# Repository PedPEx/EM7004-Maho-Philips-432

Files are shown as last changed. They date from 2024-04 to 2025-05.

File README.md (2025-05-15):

# EM7004-Maho-Philips-432 (ABORTED)
Retrofit analog interface adaptor for Maho CNC machines with a Philips 432/10 controller for use with a [Beckhoff EM7004](https://www.beckhoff.com/de-de/produkte/i-o/ethercat-klemmen/el-elm7xxx-kompakte-antriebstechnik/em7004.html) 

This project is used in the [Maho400E-LinuxCNC Retrofit project](https://github.com/PedPEx/Maho400E-LinuxCNC).

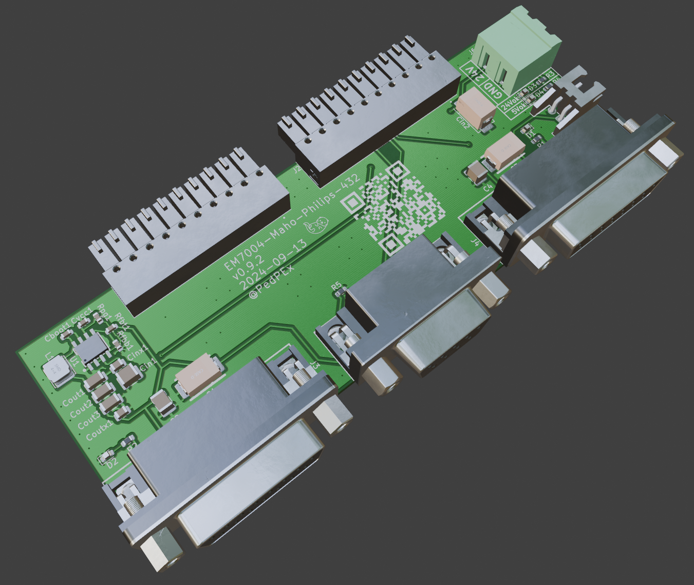
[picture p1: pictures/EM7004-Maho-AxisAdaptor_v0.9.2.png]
v0.9.2 Blender render v0.9.2


## Archiving
This project is being archived due to the EM7004 just having a 16 bit wide counter. With a travel-path of up to ~400 mm with a resolution of 1 µm a counter of at least 
```math 
n_{min} = \log_2 (\frac{400 mm}{1 \mu m}) = 18.61 bit \approx 19 bit 
```
The functionality of the rest of the PCB was not tested (BuckConverter is working). I'm sorry for everyone who had high hopes for this project or planned to use the finished product.

## Milestones
accomplished Milestones / ToDo:
- ✅ ready to go prototype at hand (v0.9.2 - corrected)
- ✅ working buck converter
- 🔲 tested with Maho axis attached
    - 🔲 working glass scale readout
    - 🔲 working Indramat speed controll

## Powering
The board needs a seperate supply voltage input to power the Philips converter-board (similar to Heidenhain EXE) for the encoders. The 5 V regulator is based around a [Texas Instruments LM33630](https://www.ti.com/product/LMR33630) and onboard. The BuckConverter part is based on the design from this [repository](https://github.com/PedPEx/BuckConverter_Enable). I recommend the [Phoenix Contact - 1962600 - TFKC 2,5/ 2-ST-5,08](https://www.phoenixcontact.com/de-de/produkte/leiterplattenstecker-tfkc-25-2-st-508-1962600) connectors to simply daisy chain all EM7004 24 V power supply lines.

## Usage
The pcb can be pretty easily assembled with standard parts of of LCSC (for furter information look at the [Online BOM](#online-preview--bom)). The connectors on the other side for plugging into the Beckhoff Module on the other hand are somewhat special. Unfortunately i found not a single alternative to the [Phoenix Contact - 1830498 - IMC 1,5/10-G-3,5 P20 THR](https://www.phoenixcontact.com/de-de/produkte/leiterplattengrundleiste-imc-1510-g-35-p20-thr-1830498) connectors, and these are not cheap at all. You can get five of them for free for testing purposes.

The first batch of boards is used in the testbench for the [Maho400E-LinuxCNC Retrofit project](https://github.com/PedPEx/Maho400E-LinuxCNC). LCSC did have a fault in the footprint files of the DB15 connectors, they were mirrored by accident. The fault has been fixed in v0.9.3 and the connectors were placed on the underside of the PCB in order to test the boards for functionality.

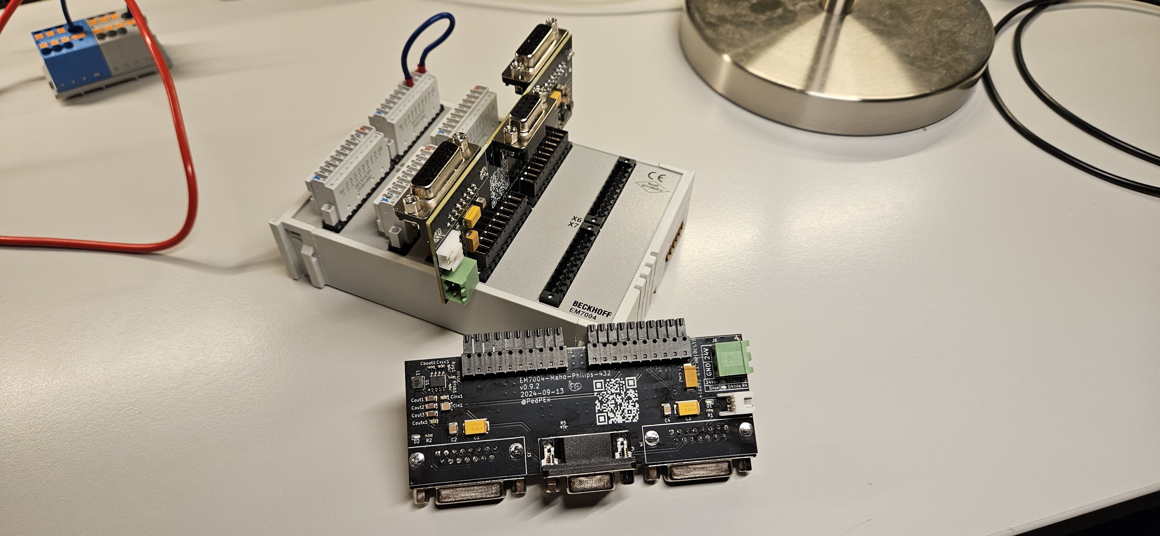
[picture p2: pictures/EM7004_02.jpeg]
EM7004_03

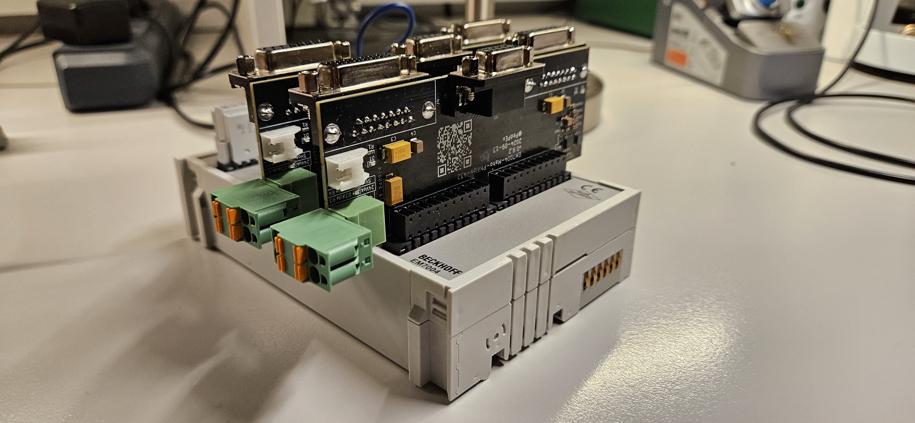
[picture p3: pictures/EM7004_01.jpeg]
EM7004_02

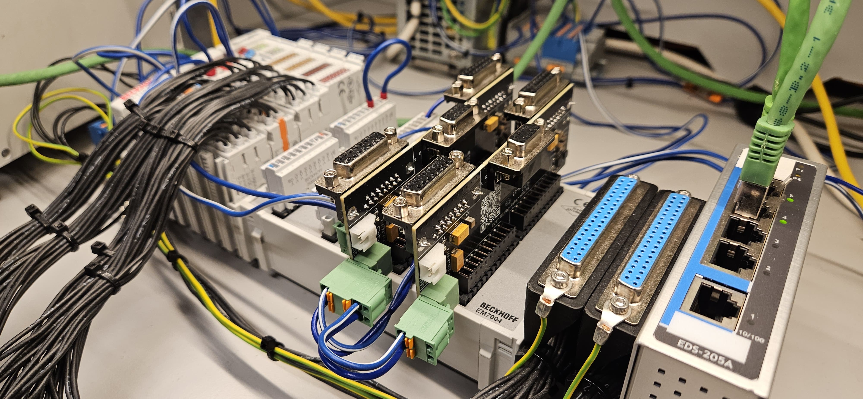
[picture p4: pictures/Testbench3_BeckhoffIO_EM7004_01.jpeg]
Testbench3_EM7004_01


## Saving costs
In order to save some money, a JST right beside the 24V input connector is provided to power other adaptors and not needing an additional buck converter onboard of the other PCBs. Just daisy chain all adaptor interfaces. The BOM needs to be adjusted accordingly for that use case (ToDo).

## Limitations
In our Maho 400E with the original Philips 432/10 controller the encoder converter card is labeled "Maho 27.69 658" on the top and no label on the bottom. It seems to be a standard Heidenhain part (Part#: 229 281 01). Example pictures are avaliable [here](https://www.cnc-shopping.com/en/philips-432-cnc-heidenhain-229-281-01-exe-platine-maho-27-69-658-3-axis-615dc0edd3849-p-5395.html). This project is specifically meant to be used with this MAHO part!

Keep in mind this adaptor is not suited for use with a standard [Heidenhain EXE 600/900](https://cncbote.de/artikel/heidenhain-exe-600-5-f-id-nr-172680a/) series converter. These need an extra 12 V supply and other connectors.

## Online Preview / BOM / Schematic
[Online BOM](https://htmlpreview.github.io/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)

[PDF Schematic](https://github.com/PedPEx/EM7004-Maho-Philips-432/blob/main/EM7004-Maho-AxisAdaptor.pdf)

## Software part
This board is meant to be used with a EM7004 module and LinuxCNC. The LinuxCNC software part can be found here: [Maho400E-LinuxCNC](https://github.com/PedPEx/Maho400E-LinuxCNC)

## Note
The pictures were rendered with the help of Blender and the [pcb2blender](https://github.com/30350n/pcb2blender) plugin and the HTML BOM was created with [InteractiveHtmlBom](https://github.com/openscopeproject/InteractiveHtmlBom).

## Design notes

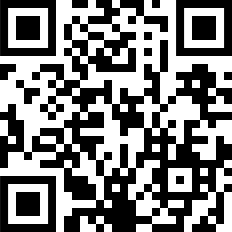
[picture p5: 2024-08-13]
pictures/QR.png

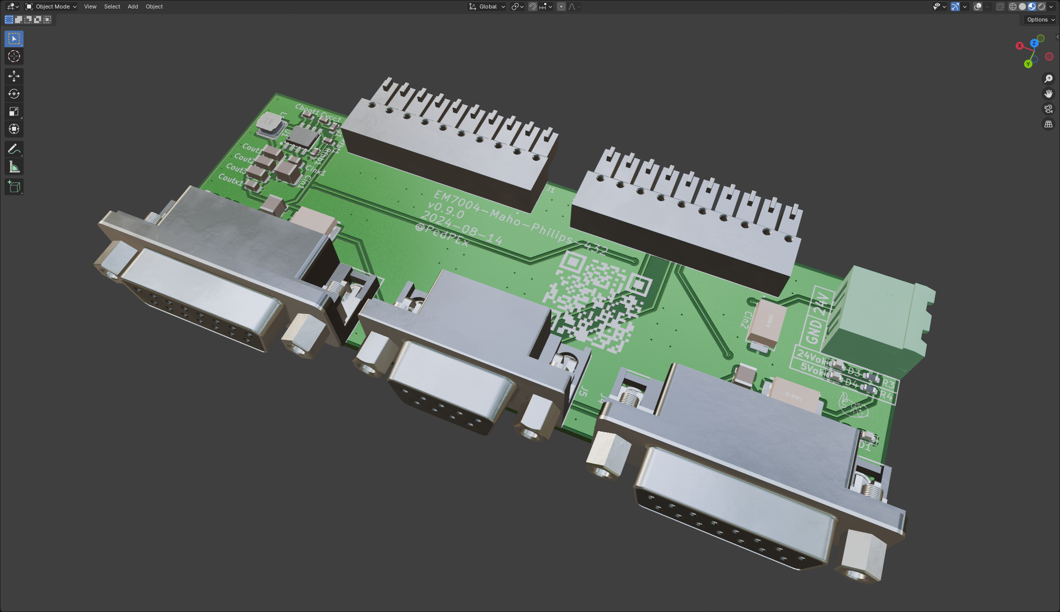
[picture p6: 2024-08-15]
pictures/EM7004-Maho-AxisAdaptor1.png

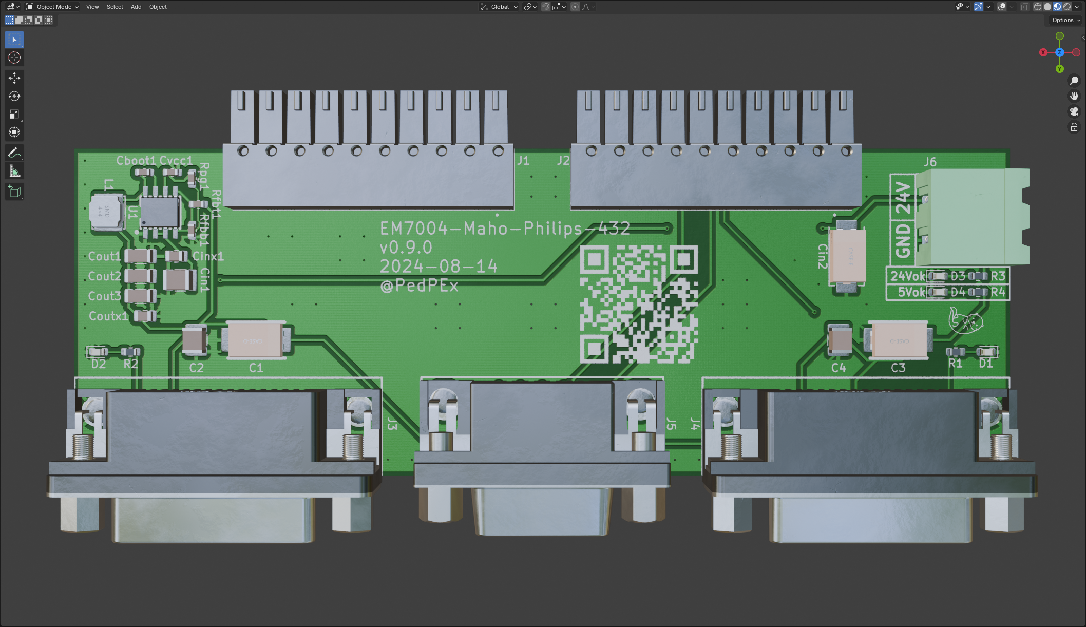
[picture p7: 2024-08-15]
pictures/EM7004-Maho-AxisAdaptor.png

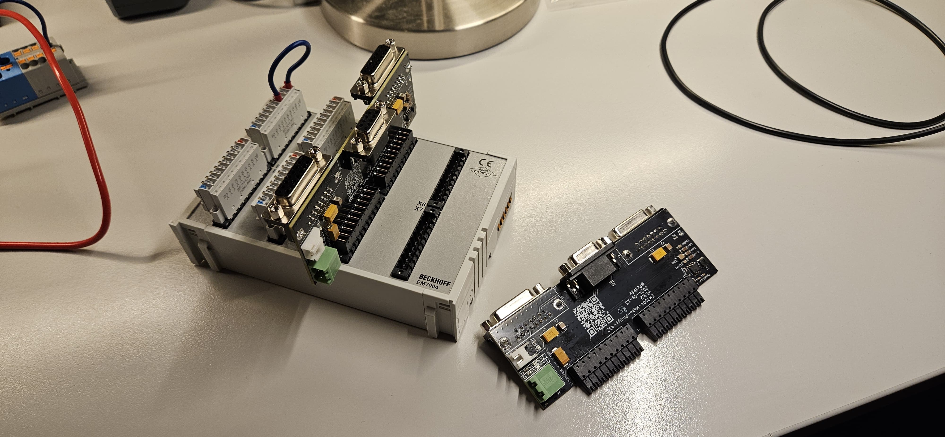
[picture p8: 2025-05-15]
pictures/EM7004_03.jpeg

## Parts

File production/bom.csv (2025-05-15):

Designator | Footprint | Quantity | Value | LCSC Part #
C1, C3 | CASE-D_7343 | 2 | 100u | C8025
C2, C4, Cin1 | 1210 | 3 | 10u | C138687
Cboot1 | 0603 | 1 | 100n | C14663
Cin2 | CAP-SMD_L7.3-W4.3-R-RD | 1 | 10u | C117038
Cinx1 | 0805 | 1 | 220n | C5378
Cout1, Cout2, Cout3 | 1206 | 3 | 47u | C412300
Coutx1 | 0805 | 1 | 100n
Cvcc1 | 0603 | 1 | 1u | C5199872
D1, D2, D3, D4 | 0603 | 4 | LED
J00, J10 | PHOENIX_1830498 | 2 | 1830498
J01, J11 | DSUB-TH_XUNPU_D-SUB-DR-15PCM-CB | 2 | D-SUB-DR-15PCM-CB | C19077338
J2 | DSUB-TH_DMR-9S | 1 | DMR-9S | C141882
J3 | CONN-TH_2P-P5.08_XY2500R-D5.08-2P | 1 | XY2500R-D-5.08-2P | C505824
J4 | CONN-TH_S2B-XH-A-1-LF-SN | 1 | S2B-XH-A-1 (LF)(SN) | C163035
L1 | IND-SMD_L4.0-W4.0 | 1 | APSWPA4018S100MTF | C5363859
R1, R2, R4 | 0603 | 3 | 680
R3 | 0603 | 1 | 4k7
R5 | 0603 | 1 | 0R
Rfbb1 | 0603 | 1 | 24k9 | C25962
Rfbt1, Rpg1 | 0603 | 2 | 100k | C25803
U1 | ESOP-8_L4.9-W3.9-P1.27-LS6.0-TL-EP | 1 | LMR33630ADDAR | C841384

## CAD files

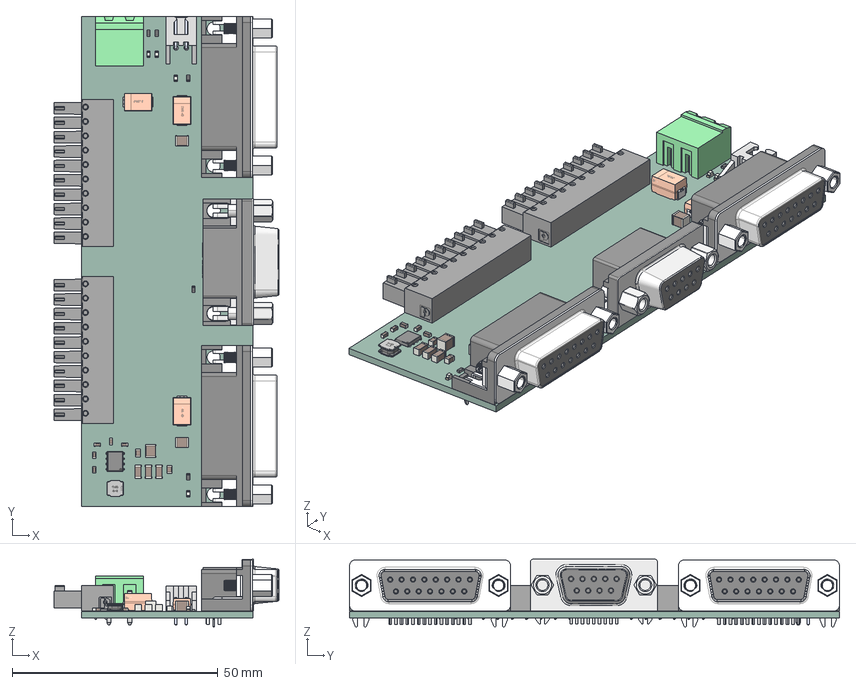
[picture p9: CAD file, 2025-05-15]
EM7004-Maho-AxisAdaptor_v093.step
54.6 x 119.2 x 16.4 mm
C_0603_1608Metric x 5
C_1206_3216Metric x 3
R_0603_1608Metric x 5
ESOP-8_L4.9-W3.9-P1.27-LS6.0-TL-EP
C_1210_3225Metric x 3
LED_0603_1608Metric x 4
C_0805_2012Metric x 2
IND-SMD_L4.0-W4.0-H1.9
DSUB-TH_DMR-9S
CASE-E_L7.3-W4.3-H4.1
CONN-TH_S2B-XH-A-1-LF-SN
CASE-D_L7.3-W4.3-H2.9 x 2
DSUB-TH_XUNPU_D-SUB-DR-15PCM-CB x 2
EM7004-Maho-AxisAdaptor_PCB

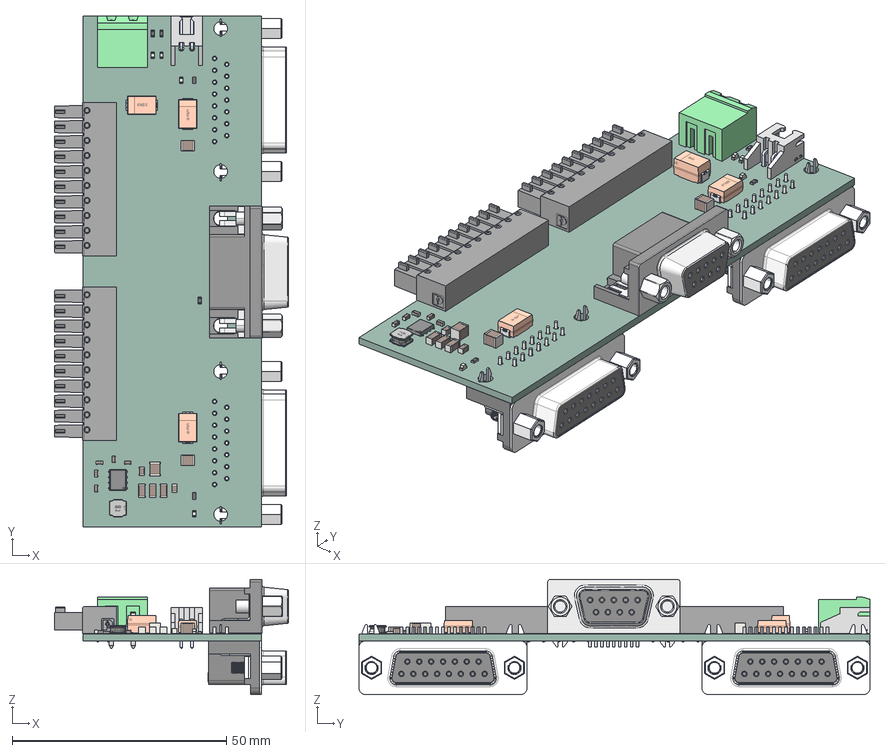
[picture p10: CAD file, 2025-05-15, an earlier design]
EM7004-Maho-AxisAdaptor_v092.step
54.6 x 119.2 x 26.9 mm
C_0603_1608Metric x 5
C_1206_3216Metric x 3
R_0603_1608Metric x 5
ESOP-8_L4.9-W3.9-P1.27-LS6.0-TL-EP
C_1210_3225Metric x 3
LED_0603_1608Metric x 4
C_0805_2012Metric x 2
IND-SMD_L4.0-W4.0-H1.9
DSUB-TH_DMR-9S
CASE-E_L7.3-W4.3-H4.1
CONN-TH_S2B-XH-A-1-LF-SN
CASE-D_L7.3-W4.3-H2.9 x 2
DSUB-TH_XUNPU_D-SUB-DR-15PCM-CB x 2
_autosave-EM7004-Maho-AxisAdaptor_PCB

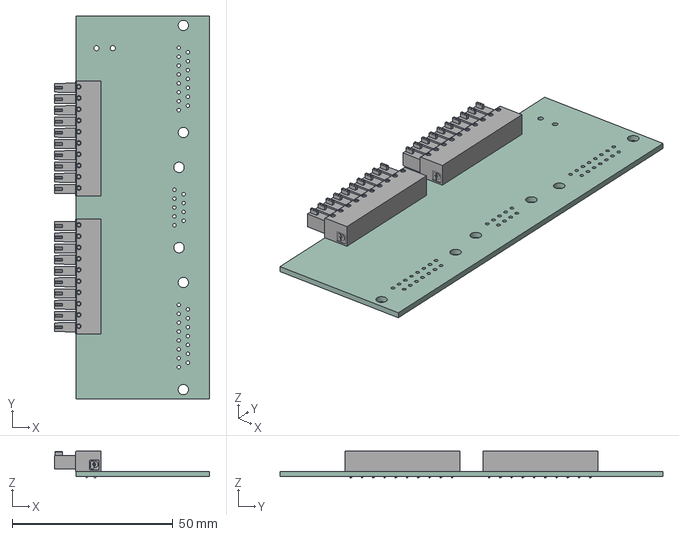
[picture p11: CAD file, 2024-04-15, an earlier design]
EM7004-Maho-AxisAdaptor.step
48.3 x 119.2 x 8.29 mm
EM7004-Maho-AxisAdaptor_PCB

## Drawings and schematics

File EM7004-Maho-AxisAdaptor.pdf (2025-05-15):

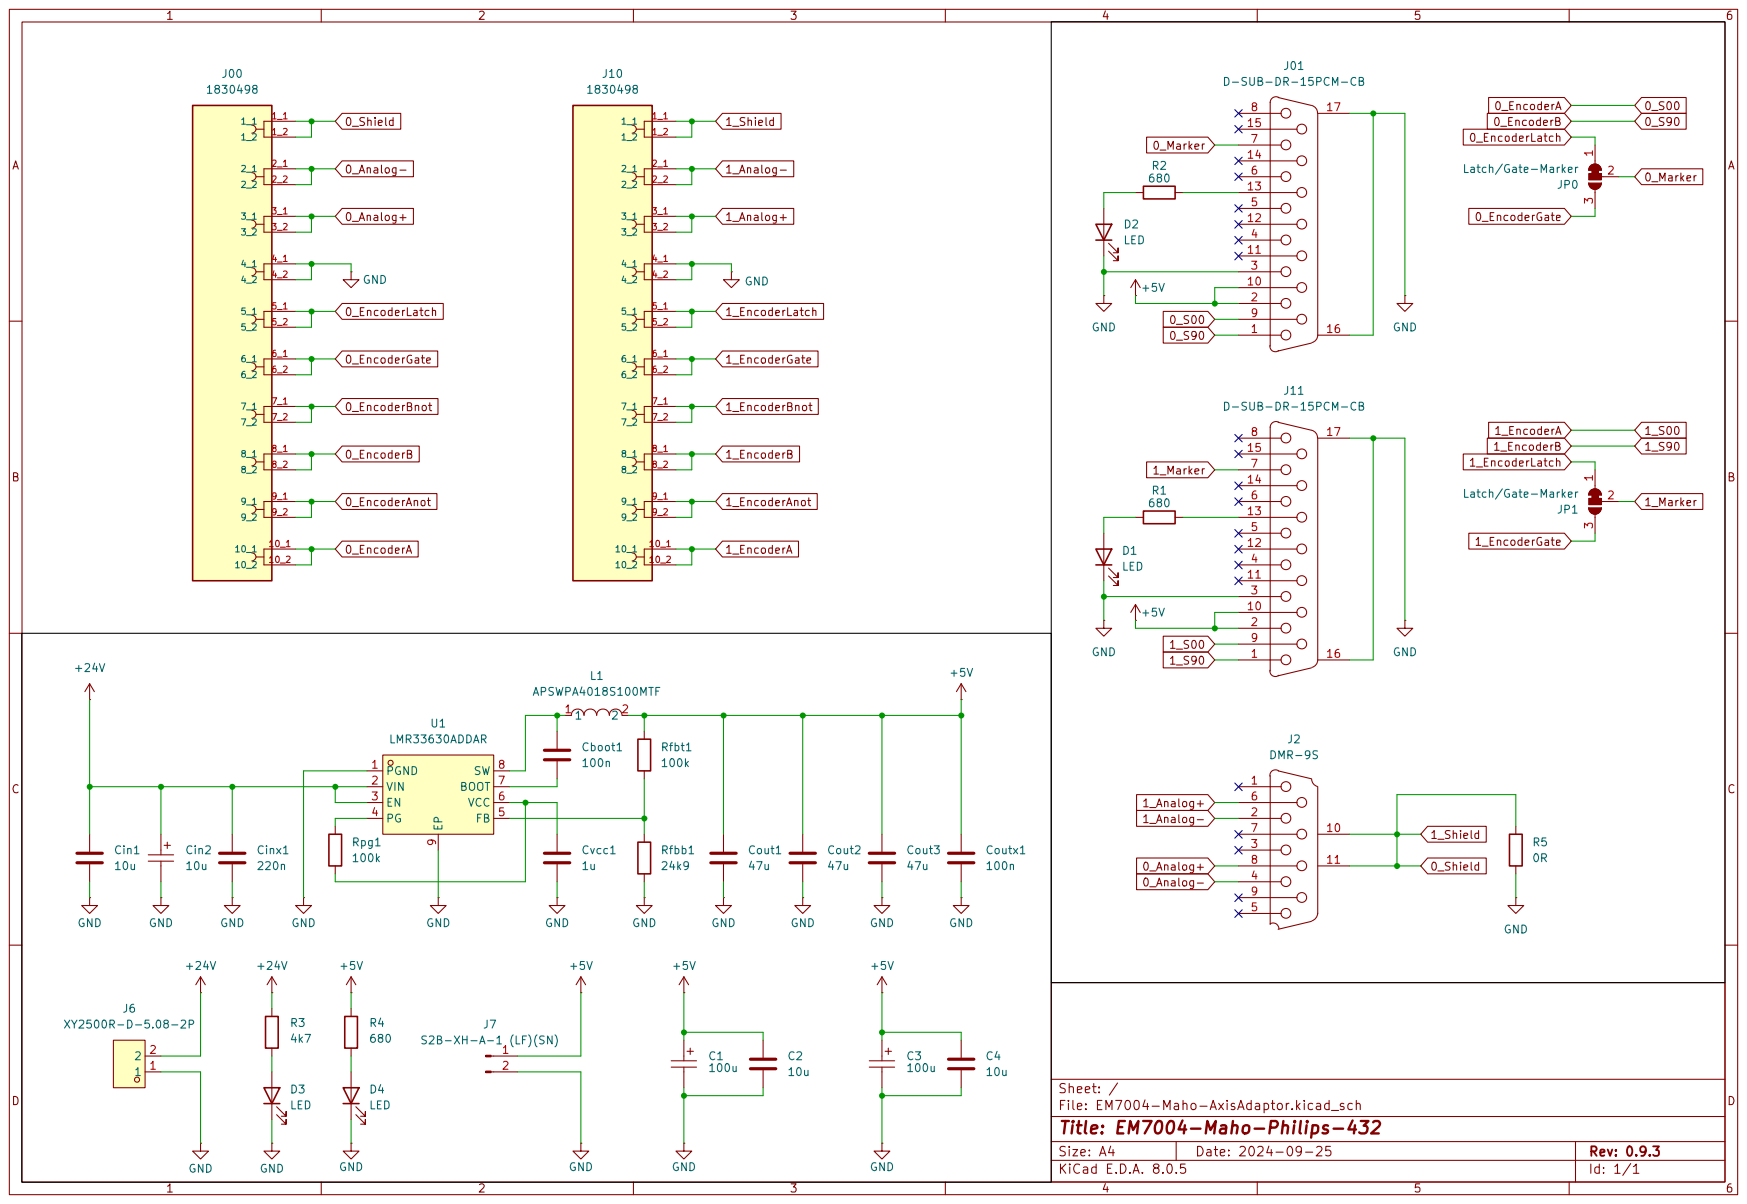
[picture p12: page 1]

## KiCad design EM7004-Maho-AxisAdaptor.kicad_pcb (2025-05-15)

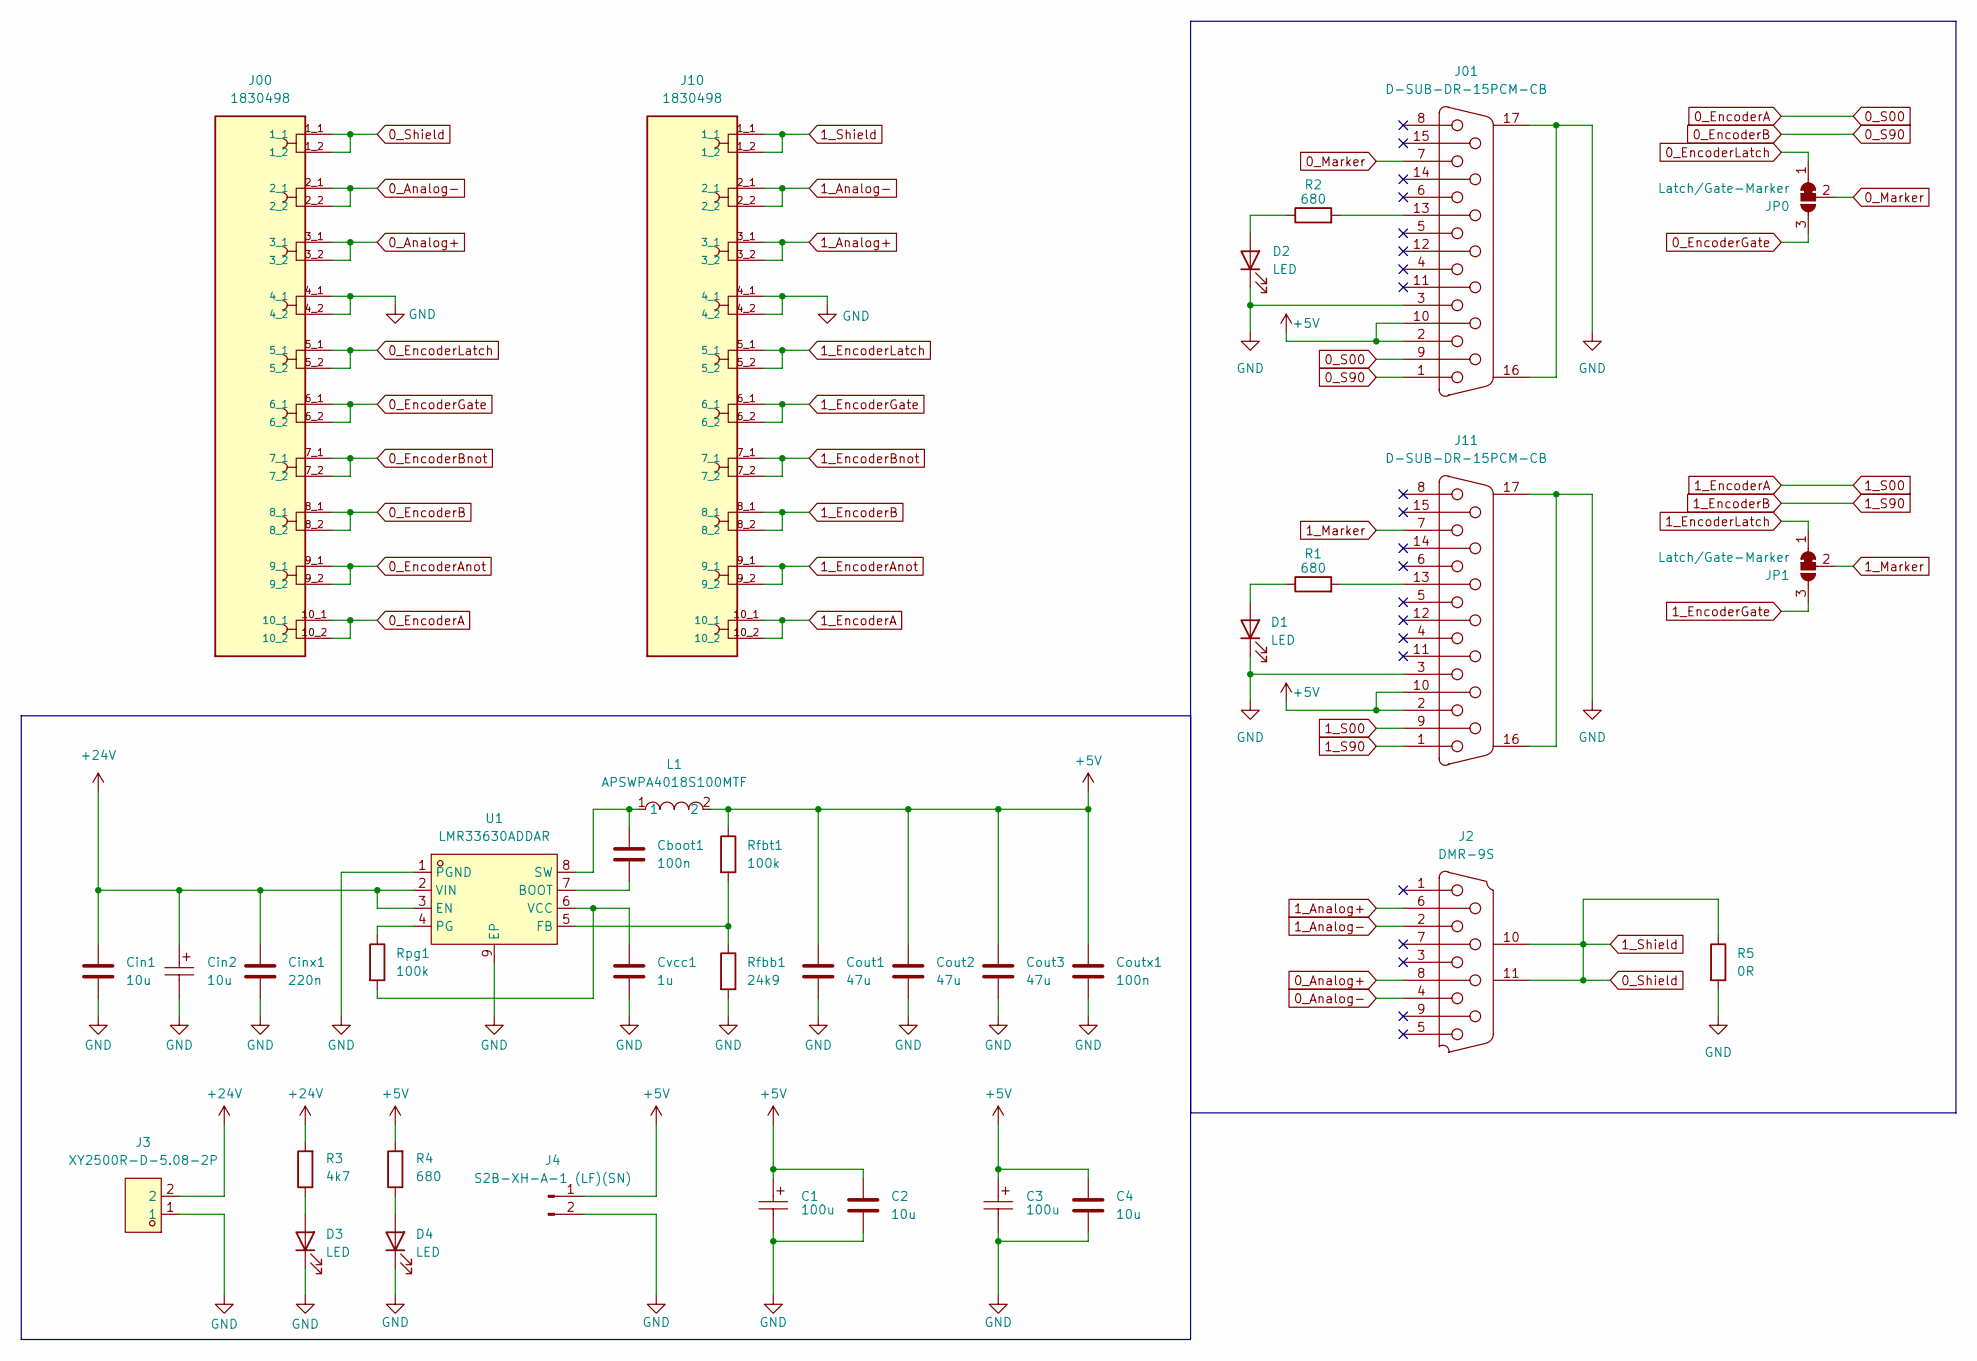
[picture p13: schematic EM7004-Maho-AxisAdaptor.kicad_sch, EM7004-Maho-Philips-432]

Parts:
C1, C3: 100u; CASE-D_7343; LCSC Part C8025
C2, C4: 10u; C_1210_3225Metric; LCSC Part C138687
Cboot1: 100n; C_0603_1608Metric; LCSC Part C14663
Cin1: 10u; C_1210_3225Metric; LCSC Part C138687
Cin2: 10u; CAP-SMD_L7.3-W4.3-R-RD; LCSC Part C117038
Cinx1: 220n; C_0805_2012Metric; LCSC Part C5378
Cout1, Cout2, Cout3: 47u; C_1206_3216Metric; LCSC Part C412300
Coutx1: 100n; C_0805_2012Metric
Cvcc1: 1u; C_0603_1608Metric; LCSC Part C5199872
D1, D2, D3, D4: LED; LED_0603_1608Metric
J00, J10: 1830498; PHOENIX_1830498
J01, J11: D-SUB-DR-15PCM-CB; DSUB-TH_XUNPU_D-SUB-DR-15PCM-CB; LCSC Part C19077338
J2: DMR-9S; DSUB-TH_DMR-9S; LCSC Part C141882
J3: XY2500R-D-5.08-2P; CONN-TH_2P-P5.08_XY2500R-D5.08-2P; LCSC Part C505824
J4: S2B-XH-A-1 (LF)(SN); CONN-TH_S2B-XH-A-1-LF-SN; LCSC Part C163035
JP0, JP1: Latch/Gate-Marker; SolderJumper-3_P1.3mm_Bridged12_Pad1.0x1.5mm
L1: APSWPA4018S100MTF; IND-SMD_L4.0-W4.0; LCSC Part C5363859
R1, R2, R4: 680; R_0603_1608Metric
R3: 4k7; R_0603_1608Metric
R5: 0R; R_0603_1608Metric
Rfbb1: 24k9; C_0603_1608Metric; LCSC Part C25962
Rfbt1: 100k; C_0603_1608Metric; LCSC Part C25803
Rpg1: 100k; C_0603_1608Metric; LCSC Part C25803
U1: LMR33630ADDAR; ESOP-8_L4.9-W3.9-P1.27-LS6.0-TL-EP; LCSC Part C841384

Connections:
0_Analog+: J00.3_1, J00.3_2, J2.8
0_Analog-: J00.2_1, J00.2_2, J2.4
0_EncoderA: J00.10_1, J00.10_2, J01.9
0_EncoderAnot: J00.9_1, J00.9_2
0_EncoderB: J00.8_1, J00.8_2, J01.1
0_EncoderBnot: J00.7_1, J00.7_2
0_EncoderGate: J00.6_1, J00.6_2, JP0.3 (B)
0_EncoderLatch: J00.5_1, J00.5_2, JP0.1 (A)
0_Marker: J01.7, JP0.2 (C)
0_Shield: J00.1_1, J00.1_2, J2.10 (MH1), J2.11 (MH2), J10.1_1, J10.1_2, R5.1
1_Analog+: J2.6, J10.3_1, J10.3_2
1_Analog-: J2.2, J10.2_1, J10.2_2
1_EncoderA: J10.10_1, J10.10_2, J11.9
1_EncoderAnot: J10.9_1, J10.9_2
1_EncoderB: J10.8_1, J10.8_2, J11.1
1_EncoderBnot: J10.7_1, J10.7_2
1_EncoderGate: J10.6_1, J10.6_2, JP1.3 (B)
1_EncoderLatch: J10.5_1, J10.5_2, JP1.1 (A)
1_Marker: J11.7, JP1.2 (C)
+5V: C1.1, C2.1, C3.1, C4.1, Cout1.1, Cout2.1, Cout3.1, Coutx1.1, J01.2, J01.10, J4.1, J11.2, J11.10, L1.2, R4.2, Rfbt1.1
+24V: Cin1.1, Cin2.1, Cinx1.1, J3.2, R3.2, U1.2 (VIN), U1.3 (EN)
GND: C1.2, C2.2, C3.2, C4.2, Cin1.2, Cin2.2, Cinx1.2, Cout1.2, Cout2.2, Cout3.2, Coutx1.2, Cvcc1.2, D1.1 (K), D2.1 (K), D3.1 (K), D4.1 (K), J00.4_1, J00.4_2, J01.3, J01.16 (MH2), J01.17 (MH1), J3.1, J4.2, J10.4_1, J10.4_2, J11.3, J11.16 (MH2), J11.17 (MH1), R5.2, Rfbb1.2, U1.1 (PGND), U1.9 (EP)
unnamed: D1.2 (A), R1.1
unnamed: D2.2 (A), R2.1
unnamed: D3.2 (A), R3.1
unnamed: D4.2 (A), R4.1
unnamed: J01.13, R2.2
unnamed: J11.13, R1.2
unnamed: Cboot1.2, U1.7 (BOOT)
unnamed: Rfbb1.1, Rfbt1.2, U1.5 (FB)
unnamed: Rpg1.1, U1.4 (PG)
unnamed: Cboot1.1, L1.1, U1.8 (SW)
unnamed: Cvcc1.1, Rpg1.2, U1.6 (VCC)

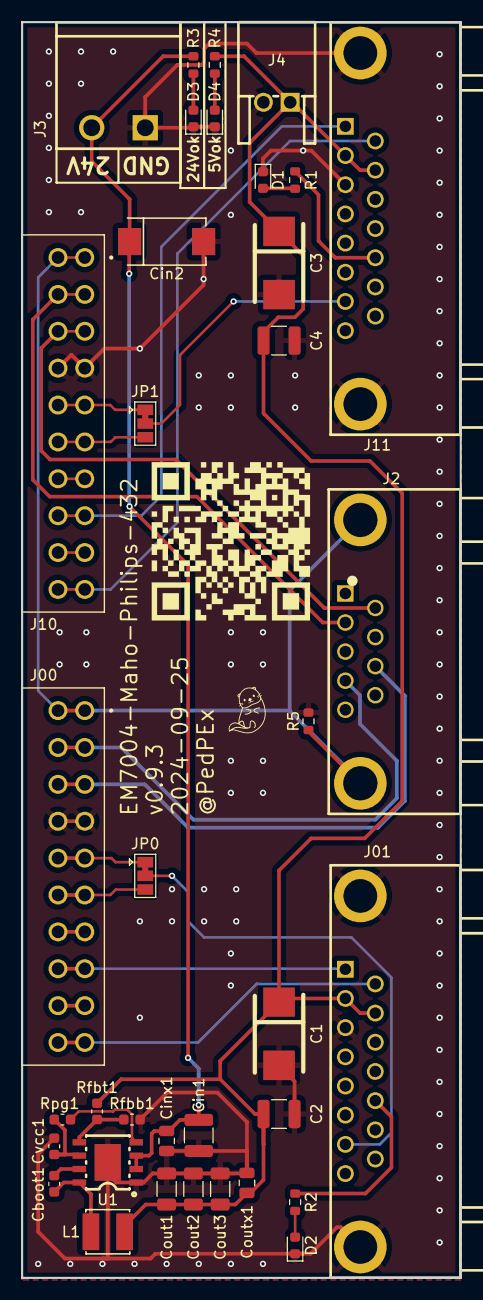
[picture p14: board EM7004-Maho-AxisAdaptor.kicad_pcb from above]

Board: 2 copper layers, 41.6 x 119.2 mm, 36 parts (0 on the bottom side), 33 nets.

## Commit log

2024-04-15 init project
    [EM7004-Maho-AxisAdaptor.kicad_pcb, EM7004-Maho-AxisAdaptor.kicad_sch]
2024-04-15 added HTML-BOM and 3D file (.step)
    [EM7004-Maho-AxisAdaptor.step]
2024-08-13 added 5V regulator
    [EM7004-Maho-AxisAdaptor.kicad_pcb, EM7004-Maho-AxisAdaptor.kicad_sch, bom.csv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]
2024-08-14 corrected LED labels
    [EM7004-Maho-AxisAdaptor.kicad_pcb]
2024-09-13 finalized v0.9.2 design
    [EM7004-Maho-AxisAdaptor.kicad_pcb, EM7004-Maho-AxisAdaptor.kicad_sch, bom.csv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]
2024-09-26 v0.9.3 - mirrored LCSC part C19077338 (DB15 connectors) was corrected
    [EM7004-Maho-AxisAdaptor.kicad_pcb, EM7004-Maho-AxisAdaptor.kicad_sch, bom.csv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]
2025-04-09 added pictures assembled & installed PCB
2025-05-15 last commit before archiving
    [EM7004-Maho-AxisAdaptor.kicad_pcb, EM7004-Maho-AxisAdaptor.kicad_sch, EM7004-Maho-AxisAdaptor_v092.step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]
